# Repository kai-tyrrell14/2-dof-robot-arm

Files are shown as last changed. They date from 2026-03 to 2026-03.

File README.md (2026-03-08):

# 2 DOF Robotic Arm
An Arduino controlled 2-dof robotic arm capable of performing autonomous pick and place commands using calibrated servos and a gripper.
## 1. Demo
Robot Arm Demo

This demonstrates a simple pick and place routine using scripted joint movements.
## 2. Features
- 2-DOF robotic arm with gripper end effector
- Smooth joint motion control
- Soft-close gripper implemented
- Multi-command serial interface
- External power supply for reliable operation
- Automated pick and place routine

## 3. Hardware
| Component | Description |
|---|---|
| Arduino Uno | Microcontroller |
| PCA9685 Motor Driver | Servo controller |
| DS3225 Servo | Shoulder joint actuator |
| MG996R Servo | Elbow joint actuator |
| MG90S Servo | Gripper actuator |
| 6V 10A Power Supply | External servo power supply |

Servos are powered through external supply while Arduino and PCA9685 are powered through USB.

## 4. System Design
The system consists of three subsystems:
### 4.1 Mechanical System
A planar system consisting of two links with a shoulder joint and an elbow joint. The gripper is the end effector used to 
pick up and place objects.
### 4.2 Electrical System
An Arduino Uno sends commands to the PCA9685 which sends PWM signals to the servos
### 4.3 Control System
Commands are entered through the serial interface which interprets the commands and converts them into servo actuation.

System diagrams are available in the 'diagrams' folder.

## 5. User Interface
Commands are sent through the Arduino Serial Monitor using the following keys:
| Command | Description |
|---|---|
| 's <μs>' | Move shoulder servo to pulse width (μs) |
| 'e <μs>' | Move elbow servo to pulse width (μs) |
| 'o' | Open gripper |
| 'c' | Close gripper |
| 'h' | Move to home position |
| 'g' | Perform pick and place routine |
| 'p' | Print current joint state |
| 'r' | Release servo PWM |
| 'wait <μs>' | Pause sequence for (μs) |

## 6. Repository Structure
An overview of the files included in this repository:
- **'/CAD':** CAD models of mechanical components
- **'/analysis':** Calibration and engineering analysis
- **'/code':** Arduino control software
- **'/diagrams':** System design diagrams
- **'/docs':** Project documentation
- **'/electronics':** Wiring diagrams and pinout reference
- **'/media':** Demomstration images and videos

## 7. Engineering Challenges
A number of issues were encountered and solutions implemented:
- Shoulder joint servo was upgraded from MG996R to DS3225 after torque requirements were not being met
- A soft-close approach was implemented to prevent servo overloading after a servo was damaged.
- Motion smoothing and sequencing was implemented after stability issues were observed.

More information can be found in 'docs/engineering_challenges.md'

## 8. Future Improvements
Some potential improvements may include:
- Improving Base Stability
- Computer Vision Integration
- Automated Path Planning

More information can be found in 'docs/future_improvements.md'

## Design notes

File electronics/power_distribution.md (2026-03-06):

# Power Distribution
**Controller:** Arduino Uno

**Servo Driver:** PCA9685

**Servo Supply:** 6V DC (10A)

## 1. Overview
The system is powered through an external 6V power supply and the arduino logic is powered through USB.
All grounds are connected and provide a common reference for PWM signalling.

See 'wiring_diagram.png' for the wiring layout.

## 2. Power Sources
| Subsystem | Voltage | Source | Notes |
|---|---|---|---|
| Arduino Uno | 5V | USB | Logic |
| PCA9685 Logic | 5V | Arduino 5V -> VCC | I2C + PWM |
| Servos | 6V | External supply -> V+ | High current load |

## 3. Power Wiring
### 3.1 Servo Power
- External +6V -> PCA9685 V+
- PCA9685 V+ rail -> Servo V+

### 3.2 Ground / Reference
- External supply GND -> PCA9685 GND
- Arduino GND -> PCA9685 GND
- Servo GND -> PCA9685 GND

## 4. Risk Controls
### 4.1 Brownout Prevention
- Servo power separate from logic power
- External supply provides stable current during peak loads

### 4.2 Gripper Overheating Prevention
- Soft-close grip implemented
- PWM is released after gripper to avoid continous stall current

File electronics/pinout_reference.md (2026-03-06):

# Pinout Reference
**Controller:** Arduino Uno

**Servo Driver:** PCA9685

Refer to 'electronics/wiring_diagram.png'.

## 1. I2C Communication Interface
| Arduino Pin | PCA9685 | Function |
|---|---|---|
| A4 | SDA | I2C Data |
| A5 | SCL | I2C Clock |
| 5V | VCC | Logic Power |
| GND | GND | Common Ground |

## 2. Servo Channel Assignments
| PCA9685 Channel | Component | Purpose |
|---|---|---|
| CH0 | Shoulder Servo | Base joint rotation |
| CH1 | Elbow Servo | Elbow joint rotation |
| CH2 | Gripper Servo | Gripper operation |

## 3. Power Distribution
| Source | Destination | Description |
|---|---|---|
| 6V External Supply | PCA9685 | Servo Power Rail |
| External GND | Arduino GND | Common Ground |
| Arduino 5V | PCA9685 | Driver Logic Power |

## 4. Servo Wiring
| Wire Colour | Signal | Connected To |
|---|---|---|
| Red | V+ | PCA9685 V+ Rail |
| Black | GND | PCA9685 GND |
| Yellow | PWM | PCA9685 Channel Output |

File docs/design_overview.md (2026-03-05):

# Design Overview
## 1. System Details
This project consists of a small two degrees-of-freedom robotic arm capable of performing pick and place tasks. The arm
involves two rotational joints, the shoulder and elbow, and an end effector, the gripper. The system is controlled using an
Arduino Uno and a PCA9685 PWM motor driver which generates the servo control signals. The arm is capable of moving small objects, such as a dice, to from from predetermined positions using scripted joint movements.

## 2. Mechanical Design
The arm consists of two links which rotate about a stationary base. The links are driven at two joints through servo motors.
The gripper attached to the end of the second link is also driven by a servo motor.

The servo motors used are:
- Shoulder Joint: DS3225
- Elbow Joint: MG996R
- Gripper: MG90S

The shoulder joint is driven directly by the servo, while the elbow joint is driven through a pulley system.

## 3. Electrical Design
The system's electronics consist of:
- Arduino Uno microcontroller
- PCA9685 motor driver
- External 6V 10A power supply
- USB power supply

The Arduino Uno and PCA9685 are powered by the USB supply and control the systems logic. The PCA9685 provides PWM signals to the servos which are powered through the external 6V 10A power supply.

## 4. Control Design
The arm is controlled through commands entered into the serial interface which the code interprets and provides PWM commands through the arduino to the PCA9685 to the servos to perform the commanded tasks. The system allows for specific poses and positions to be saved and used to perform different routines, such as the pick and place routine.

## 5. Key Design Decisions
The following design decisions were implemeted to ensure the reliability and performance of the system:
- A PCA9685 motor driver was used to provide accurate and stable servo timing.
- Servo limits were calibrated to prevent mechanical binding and damage to servos.
- A soft-close approach was used to control the gripper and prevent overloading the servo.
- The logic power and servo actuation power were separated into their own circuits to prevent voltage drop and overloading of
  the arduino.

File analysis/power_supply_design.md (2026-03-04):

# Power Supply Design
This document outlines the power requirements for the entire robotic arm system. The system incorporates three different servo
types for the shoulder, elbow and gripper.

## 1. System Components
| Component | Supply | Notes |
|---|---|---|
| Arduino Uno | USB | Microcontroller |
| PCA9685 | Arduino 5V | PWM Driver |
| Shoulder Servo | 6V External | DS3225 Servo |
| Elbow Servo | 6V External | MG996R Servo |
| Gripper Servo | 6V External | MG90S Servo |

## 2. Estimated Servo Current
Current drawn by servos varies depending on load.
| Condition | DsS3225 (Shoulder) | MG996R (Elbow) | MG90S (Gripper) |
|---|---|---|---|
| Idle | ~20-50 mA | ~10-50 mA | ~10-20 mA |
| Moving (no load) | ~500 mA | ~500-900 mA | ~150-250 mA |
| Under Load | ~1.5 A | ~1.5-2 A | ~400-600 mA |
| Stall (worst case) | ~2.3 A | ~2.5 A | ~700 mA |

## 3. Worst Case Design Scenario
The worst case design scenario assumes all servos acting at stall conditions.
Worst case per servo:
- Shoulder (DS3225) = 2.3 A
- Elbow (MG996R) = 2.5 A
- Gripper (MG90S) = 0.7 A

Total peak demand:
2.3 A + 2.5 A + 0.7 A = 5.5 A

## 4. Logic Power Requirements
| Component | Current |
|---|---|
| Arduino Uno | ~50 mA |
| PCA9685 | ~10 mA |
Total pwer requirement ≈ 60 mA

## 5. Final Power Supply Design 
The final design for delivering power to the robotic arm involves separating servo actuation power and logic power into two
different circuits. This prevents voltage drop and ensures the Arduino Uno or PCA9685 do not draw excessive current. The power
must also safely meet the demands of the worst case design scenario.

The following power supplys are used in the system:
- Servo Actuation Power: External 6V 10A power supply
- Logic Power: USB powered

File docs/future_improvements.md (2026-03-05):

# Future Improvements
This document outlines potential improvements that could be implemented to increase the performance and functionality of the
robotic arm.
## Increased Base Stability
The stability of the base could be increased by increasing the weight of the base or rigidly attaching the base to a stable surface.
## Computer Vision Integration
Adding a camera and computer vision system would allow the system to detect objects and pick and place them, rather then 
rely on known positions.
## Automated Path Planning
Currently shoulder and elbow movement are performed sequentially, by adding path planning the arm would be able to move to certain locations in the most efficient manner with smoother motion.

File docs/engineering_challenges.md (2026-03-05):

# Engineering Challenges
This document summarises the main engineering challenges faced during the development of the robotic arm and the solutions that
were implemented.

## 1. Shoulder Torque Limitation
### 1.1 Issue
During the early testing of the shoulder joint, once link 2 was connected the joint struggled when rotated by a low torque servo.
### 1.2 Cause
Adding link 2 increases the torque requirements to rotate the shoulder joint.
### 1.3 Solution
The inital MG996R servo was upgraded to a higher torque DS3225 servo which provided the required torque and ensured stable
motion.

## 2. Gripper Servo Overloaded
### 2.1 Issue
During the initial testing of the gripper servo there was audible strain and eventually the servo failed and needed to be replaced.
### 2.2 Cause
The gripper servo was commanded to close past its limits and when gripping an object it attempts to close to this point which overloads the servo and causes permanent damage.
### 2.3 Solution
A soft-close approach was implemented in the code for gripper which prevents the gripper from loading past its limits and 
releases the servo to prevent overloading.

## 3. Arm Stability
### 3.1 Issue
The arm occasionally tipped forward when elbow was fully extended.
### 3.2 Cause
When fully extended the moment arm is increased which reduces the stability of the arm's base.
### 3.3 Solution
Motion sequencing and smoothing were implemented to increase stability.

## 4. Command Interface
### 4.1 Issue
Early versions of the code required single codes to be entered one at a time.
### 4.2 Cause
The command interface didn't support the entry of multiple commands.
### 4.3 Solution
A command splitter was implemented, allowing for the entry of a series of commands which could be performed sequentially.

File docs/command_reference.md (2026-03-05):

# Command Reference
This document outlines how to control the arm through the serial interface.
## 1. Command Format
Commands to the arm are entered through Arduino's Serial Monitor. Multiple commands can be performed in sequence by separating
them  with ':'.

For example:

s 1400; e 1200; h

## 2. Supported Commands
| Command | Description |
|---|---|
| 's <μs>' | Move shoulder servo to pulse width (μs) |
| 'e <μs>' | Move elbow servo to pulse width (μs) |
| 'o' | Open gripper |
| 'c' | Close gripper |
| 'h' | Move to home position |
| 'g' | Perform pick and place routine |
| 'p' | Print current joint state |
| 'r' | Release servo PWM |
| 'wait <μs>' | Pause sequence for (μs) |

## 3. Example Commands
s 1400; e 1300; o;

Moves shoulder and elbow to respective positions and opens gripper.

s 1700; e 1600; h; g
Moves shoulder and elbow to respective positions, returns home, performs pick and place routine.

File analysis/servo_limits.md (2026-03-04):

# Servo Limits Calibration
All limits were determined experimentally using incremental increases to determine where overloading occurs.

## 1. Summary Table
| Joint | Channel | Min (μs) | Max (μs) | Home (μs) | 
|---|---|---|---|---|
| Shoulder | CH0 | 700 | 2300 | 1200 |
| Elbow | CH1 | 700 | 1700 | 800 |
| Gripper | CH2 | 500 (open) | 950 (soft-close) | 950 |

## 2. Calibration Method
1. Servo was moved in small increments (5-10 μs).
2. Movement was stopped as soon as binding occured.
3. Limits were set 50 μs from these points to ensure safe limits.
4. These limits were then validated through repeated motion.
5. These final values were set as constraints in the code.

## 3. Design Intent

These servo limits are clearly defined and documented in order to:
- Prevent mechanical binding
- Prevent servo overloading
- Prevent gear stripping
- Ensure system reliability

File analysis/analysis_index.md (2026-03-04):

# Analysis Index
The files in this folder outline the calibration and analysis methods used in the design of the robotic arm.

## 1. Key Outcomes
- Calibrated safe servo operating limits and ensured constraints in code.
- After overloading a servo resulting in damage, a soft-close was implemented for the gripper.
- Resolved potential tipping risks by ensuring proper order of servo actuation.

## 2. Documents
- 'servo_limits.md' : Outlines final servo pulse ranges and home position.
- 'calibration_results.md' : Summarises calibration testing, constraints and validation.
- 'power_supply_design.md' : Estimated current demand for servo power distribution.
- 'stability_notes.md' : Observed behaviour of robot arm stability and when tipping may occur.

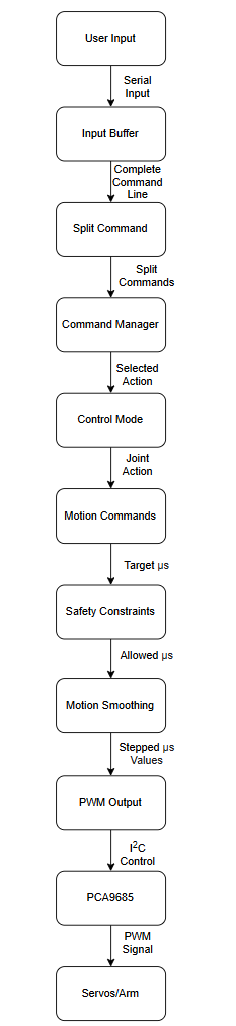
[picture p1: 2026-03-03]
diagrams/control_architecture.png

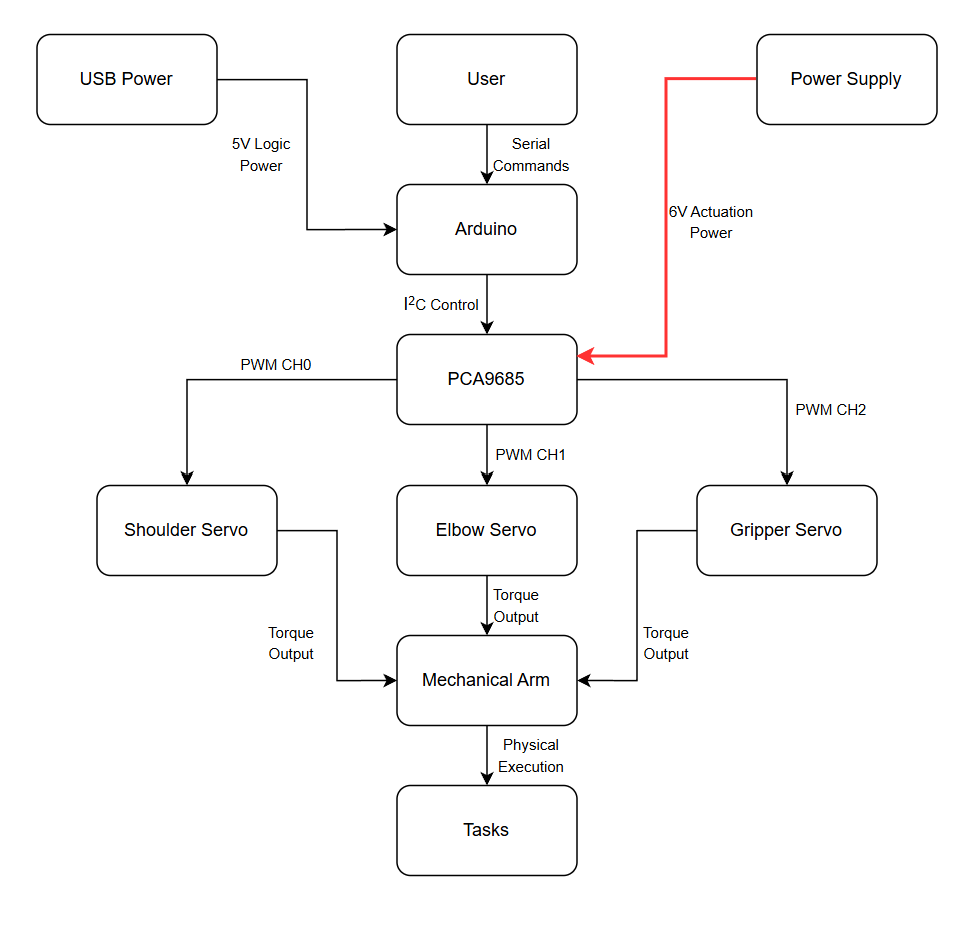
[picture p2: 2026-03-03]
diagrams/system_block_diagram.png

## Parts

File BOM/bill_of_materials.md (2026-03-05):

# Bill of Materials
| Item | Component | QTY |
|---|---|-----|
| 1 | 3D Printed Parts | 1 set |
| 2 | Arduino Uno | 1 | 
| 3 | PCA9685 Motor Driver | 1 |
| 4 | DS3225 Servo | 1 |
| 5 | MG996R Servo | 1 |
| 6 | MG90S Servo | 1 |
| 7 | 8mm Shaft | 1 |
| 8 | 5mm Shaft | 1 |
| 9 | 608 Bearing | 2 |
| 10 | 625 Bearing | 2 |
| 11 | 25T Metal Round Servo Horn | 1 |
| 12 | Servo Spline Shaft | 1 |
| 13 | GT2 Timing Belt | 1 |
| 14 | 20T GT2 Pulley | 1 |
| 15 | 40T GT2 Pulley | 1 |
| 16 | 5mm Shaft Collar | 2 |
| 17 | 8mm Shaft Coupling | 1 |
| 18 | 5mm Shaft Coupling | 1 |
| 19 | Gripper | 1 |
| 20 | M3 Screws & Nuts | Various |
| 21 | 6V 10A Power Supply | 1 |

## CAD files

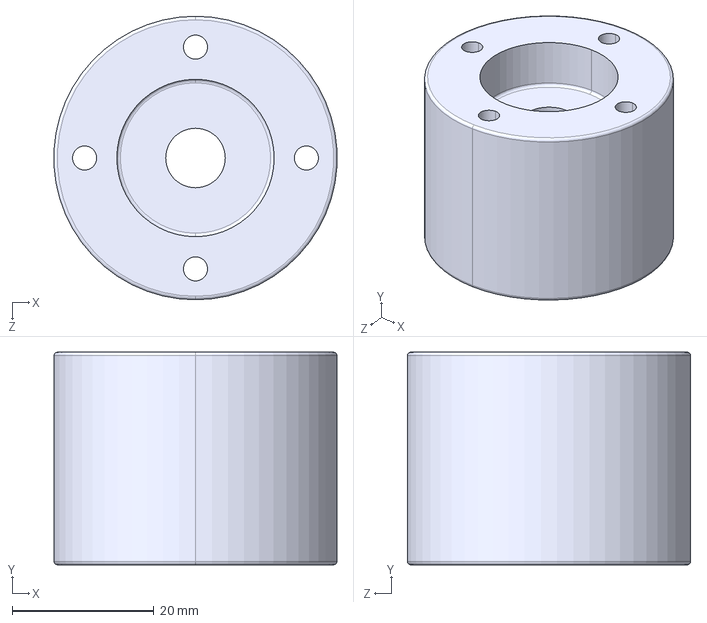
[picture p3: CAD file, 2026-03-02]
CAD/exports/bearing_tower.STEP
39.9 x 30.0 x 40.0 mm

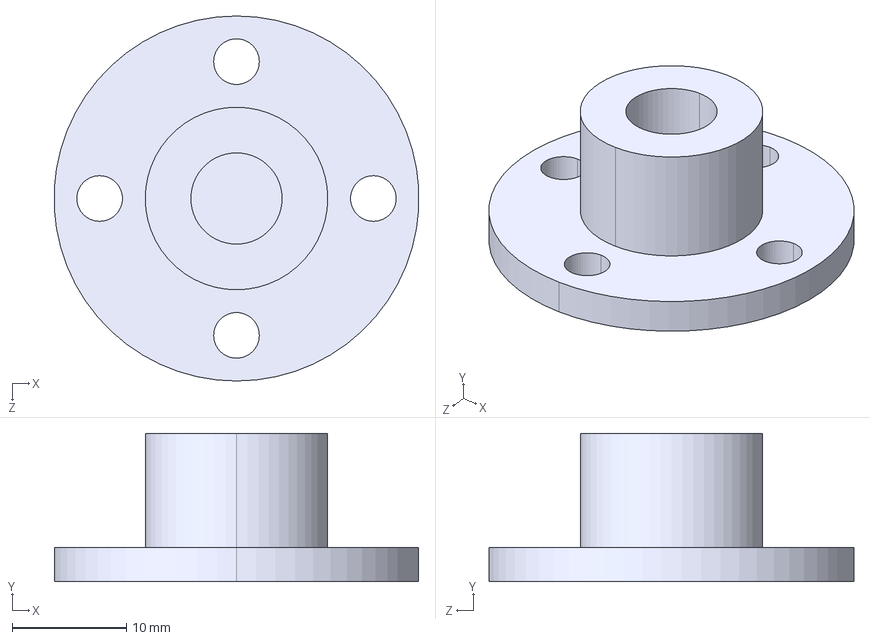
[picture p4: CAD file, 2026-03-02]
CAD/exports/shaft_hub_base.STEP
32.0 x 13.0 x 32.0 mm

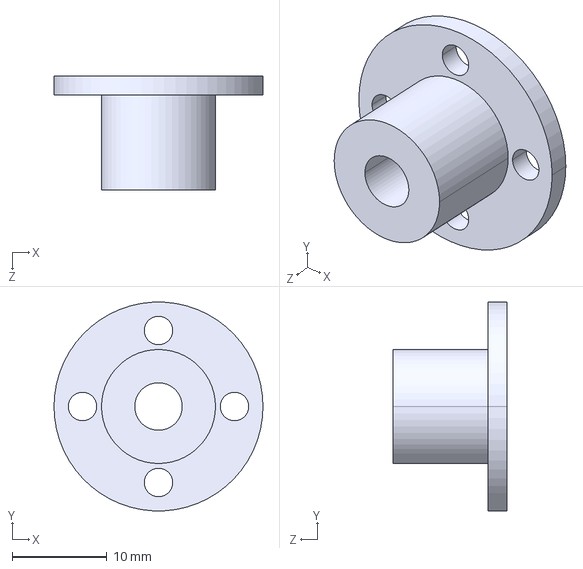
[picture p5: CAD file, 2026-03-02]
CAD/exports/link_2_shaft_hub.STEP
22.0 x 22.0 x 12.0 mm

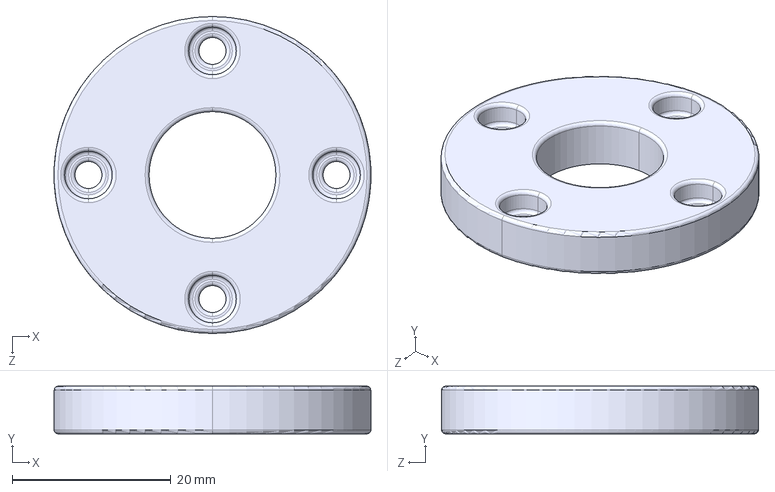
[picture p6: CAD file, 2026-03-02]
CAD/exports/top_retainer_plate.STEP
40.0 x 6.00 x 40.0 mm

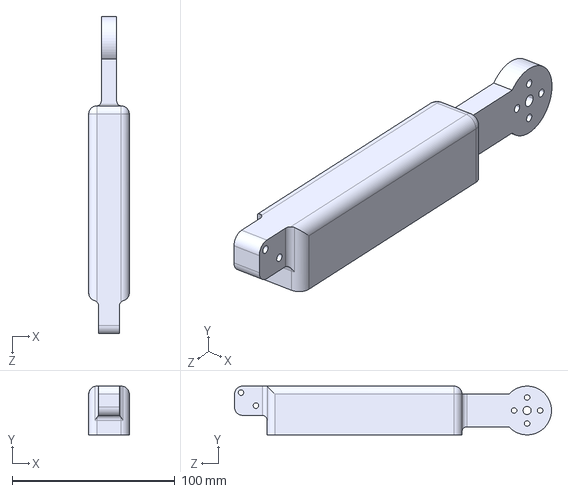
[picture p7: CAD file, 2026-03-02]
CAD/exports/link_2.STEP
25.0 x 30.0 x 195.0 mm

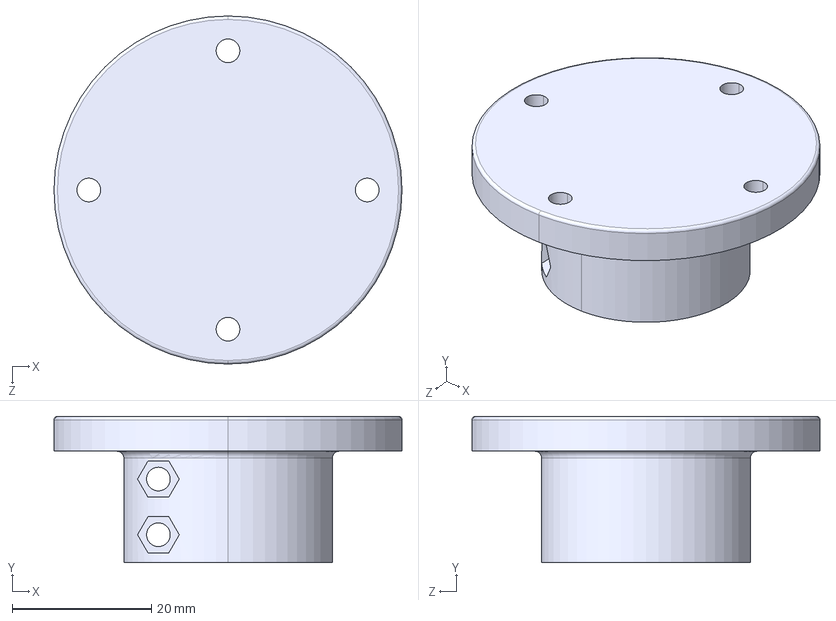
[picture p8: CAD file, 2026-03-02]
CAD/exports/link_1_shaft_hub.STEP
50.0 x 21.0 x 50.0 mm

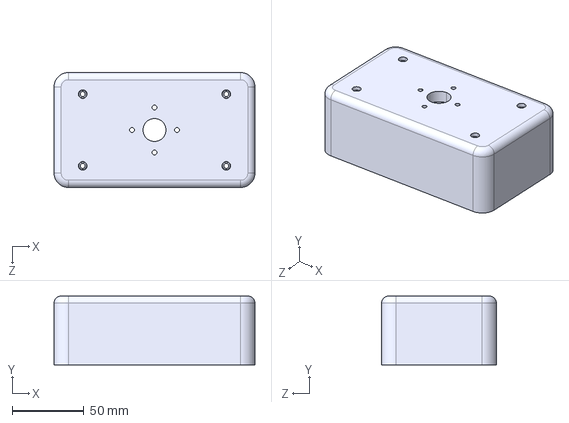
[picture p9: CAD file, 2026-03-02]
CAD/exports/base_plate_top.STEP
140.0 x 48.0 x 80.0 mm

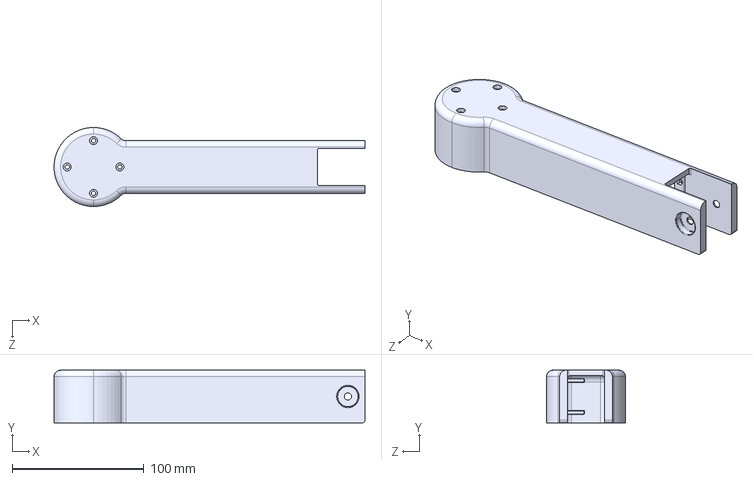
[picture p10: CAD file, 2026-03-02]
CAD/exports/link_1.STEP
236.0 x 40.0 x 60.0 mm

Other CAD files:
CAD/exports/base_plate_bottom.STEP
CAD/parts/base_plate_bottom.SLDPRT
CAD/parts/base_plate_top.SLDPRT
CAD/parts/bearing_tower.SLDPRT
CAD/parts/link_1.SLDPRT
CAD/parts/link_1_shaft_hub.SLDPRT
CAD/parts/link_2.SLDPRT
CAD/parts/link_2_shaft_hub.SLDPRT
CAD/parts/shaft_hub_base.SLDPRT
CAD/parts/top_retainer_plate.SLDPRT

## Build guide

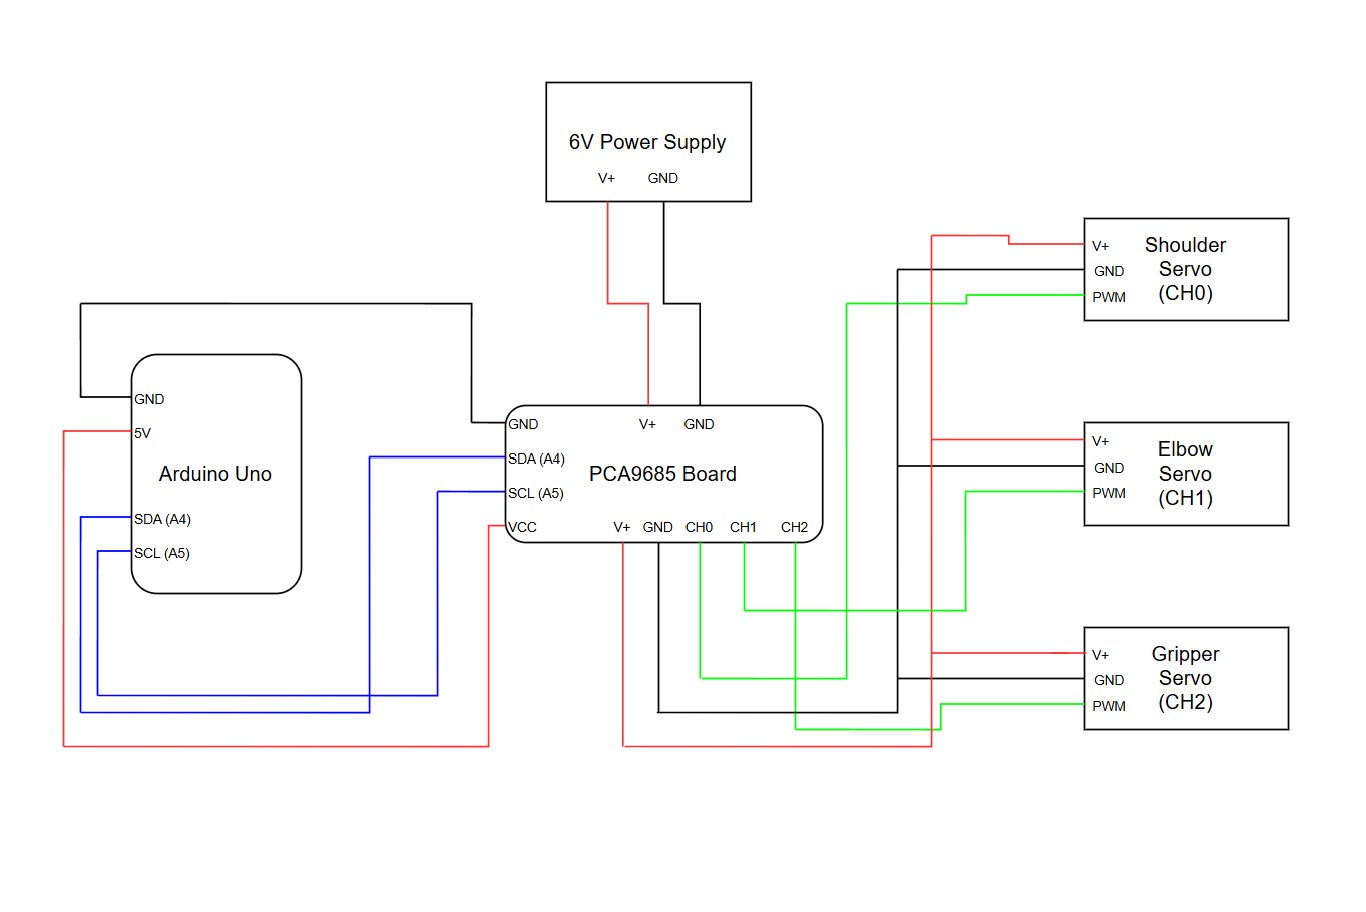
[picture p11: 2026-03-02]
electronics/wiring_diagram.png

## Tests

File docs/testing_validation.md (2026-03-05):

# Testing Validation
This document outlines he methods to verify the system works as expected.
## 1. Testing Objectives
The objectives that were tested and verified:
- Each joint could move through its calibrated servo limits
- Joint movements were performed smoothly
- Small objects could be gripped and released
- The pick and place routine was performed correctly
- The system can operate without any damage to or overheating of servos

## 2. Testing Procedures
The system was tested through the serial interface.

Manual commands were entered to test each servo through their calibrated ranges and multiple open and close gripper commands
were performed.

Repeated automated pick and place routines were then executed to ensure motion and positioning were accurate and repeatable.

## 3. Testing Results
| Test | Descritption | Results |
|---|---|---|
| Joint Movement | Shoulder and elbow moved through calibrated servo limits| Pass |
| Smooth Motion | Servos moved smoothly without sudden jumps | Pass |
| Gripper Operation | Object successfully gripped and released | Pass |
| Pick and Place Routine | The pick and place routine performed multiple times in succession | Pass |

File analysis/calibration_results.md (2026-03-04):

# Calibration Results
This document summarises the methods for calibrating the servos used for the robotic arm. 
This calibration was necessary before automated routines, such as pick and place, can be performed.

## 1. Test Method
- Controller: Arduino Uno + PCA9685
- Method: incremental pulse stepping
- Observation criteria: mechanical binding, audible strain, overheating
- Validation: repeated motion cycles without any issues

Final operating limits shown in 'servo_limits.md'
## 2. Calibration of Servos
### 2.1 Shoulder (CH0)
**Experimental range:** 600-2400 μs

**Key observations:**
- Binding observed below 640 μs
- Binding observed above 2350 μs
- Shoulder movement at high speeds with elbow fully extended may result in tipping

**Validation:**
- Repeated motion cycles within servo limits resulted in no binding

### 2.2 Elbow (CH1)
**Experimental range:** 600-1800 μs

**Key observations:**
- Increasing the pulse width moves elbow downwards
- Binding observed below 650 μs
- Binding observed above 1770 μs

**Validation:**
- Repeated motion cycles within servo limits resulted in no binding

### 2.3 Gripper (CH2)
**Initial issue:**
- Original command for closing gripper resulted in sustained overloading of the SG90 servo
- As a result one servo failed from being overloaded for too long
- Gripper was driven to stall torque near limit

**Resolution:**
- A soft-close was implemented which closes the gripper enough to grip an object, before releasing the servo to prevent extended overloading

**Validation:**
- Repeated grip and release cycles with soft-close without failure

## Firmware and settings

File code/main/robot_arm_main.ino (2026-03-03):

#include <Wire.h>
#include <Adafruit_PWMServoDriver.h>

Adafruit_PWMServoDriver pwm(0x40);

// Channels
// Channels mapped as per 'pinout_reference.md' so to change channels only these values 
// must be changed.
#define SHOULDER_CH 0
#define ELBOW_CH    1
#define GRIPPER_CH  2

// Limits
// Limits have been determined experimentally, where going past these limits can overload
// servos.
const int SHOULDER_MIN_US = 700;
const int SHOULDER_MAX_US = 2300;

const int ELBOW_MIN_US = 700;
const int ELBOW_MAX_US = 1700;

const int GRIP_OPEN_US       = 500;
const int GRIP_CLOSE_SOFT_US = 950;

// Home Position
// This position is used as a reference for testing and demonstrations.
const int SHOULDER_HOME_US = 1200;
const int ELBOW_HOME_US    = 800;

// The auto settings allow for faster movements to known positions, such as home or pick
// and place. The manual settings are slower for manual inputs.
const int AUTO_STEP_US   = 10;  
const int AUTO_DELAY_MS  = 10;

const int MANUAL_STEP_US  = 5;  
const int MANUAL_DELAY_MS = 4;

// Initial Position
int sh_us = SHOULDER_HOME_US;
int el_us = ELBOW_HOME_US;
int gr_us = GRIP_CLOSE_SOFT_US;

// Poses
struct Pose { int shoulder; int elbow; };

Pose HOME       = { 1200,  800 };
Pose ABOVE_PICK = { 1200, 1200 };  
Pose PICK_DOWN  = { 1200, 1700 };  

Pose ABOVE_PLACE= { 1500, 1200 };  
Pose PLACE_DOWN = { 1500, 1700 };

Pose LIFT_PICK  = { 1200, 1050 };  
Pose LIFT_PLACE = { 1500, 1050 };  


// Converts microseconds to ticks to allow for consistent pulse widths through each channel.
int usToTicks(int us) {
  us = constrain(us, 400, 2500);
  return (int)((us * 4096L) / 20000L);  
}

// Uses the value above to set the PWM for the servos, where the limits and positions
// above can be changed with changing logic below.
void setServoUs(int ch, int us) {
  pwm.setPWM(ch, 0, usToTicks(us));
}

// Releases servo to prevent overloading.
void releaseServo(int ch) {
  pwm.setPWM(ch, 0, 0);
}

// Using the stepped motion below, sudden acceleration and peak torque are reduced.
void moveTo(int ch, int &current, int target, int stepUs, int delayMs) {
  target = constrain(target, 400, 2500);

  if (target > current) {
    for (int u = current; u <= target; u += stepUs) {
      setServoUs(ch, u);
      delay(delayMs);
    }
  } else {
    for (int u = current; u >= target; u -= stepUs) {
      setServoUs(ch, u);
      delay(delayMs);
    }
  }
  current = target;
}

void printState() {
  Serial.print("Shoulder_us="); Serial.print(sh_us);
  Serial.print("  Elbow_us=");  Serial.print(el_us);
  Serial.print("  Gripper_us=");Serial.println(gr_us);
}

// The code below sets the order of movement. The elbow is moved before the shoulder to 
// reduce the risk of the arm tipping.
void moveArm(Pose p, bool elbowFirst=true) {
  p.shoulder = constrain(p.shoulder, SHOULDER_MIN_US, SHOULDER_MAX_US);
  p.elbow    = constrain(p.elbow,    ELBOW_MIN_US,    ELBOW_MAX_US);

  if (elbowFirst) {
    moveTo(ELBOW_CH,    el_us, p.elbow,    AUTO_STEP_US, AUTO_DELAY_MS);
    moveTo(SHOULDER_CH, sh_us, p.shoulder, AUTO_STEP_US, AUTO_DELAY_MS);
  } else {
    moveTo(SHOULDER_CH, sh_us, p.shoulder, AUTO_STEP_US, AUTO_DELAY_MS);
    moveTo(ELBOW_CH,    el_us, p.elbow,    AUTO_STEP_US, AUTO_DELAY_MS);
  }
}

void gripperOpen() {
  moveTo(GRIPPER_CH, gr_us, GRIP_OPEN_US, AUTO_STEP_US, AUTO_DELAY_MS);
  releaseServo(GRIPPER_CH);
}

// This function ensures that the gripper is able to pick up an object with overloading and
// damaging the servo.
void gripperCloseSoft(int holdMs = 150) {
  int approach = (GRIP_OPEN_US + GRIP_CLOSE_SOFT_US) / 2;
  moveTo(GRIPPER_CH, gr_us, approach, AUTO_STEP_US, AUTO_DELAY_MS);
  delay(60);

  moveTo(GRIPPER_CH, gr_us, GRIP_CLOSE_SOFT_US, AUTO_STEP_US, AUTO_DELAY_MS);
  // This delay ensures that the gripper properly grips the object.
  delay(holdMs);
  // This release prevents holding for too long and overloading.
  releaseServo(GRIPPER_CH);
}

// Pick and Place Routine
// Repeatable sequence for testing and demonstration.
void runPickPlace() {
  moveArm(ABOVE_PICK, true);  delay(150);
  gripperOpen();              delay(120);

  moveArm(PICK_DOWN, false);  delay(180);
  gripperCloseSoft(180);      delay(120);

  moveArm(LIFT_PICK, true);   delay(150);

  moveArm(ABOVE_PLACE, true); delay(150);

  moveArm(PLACE_DOWN, false); delay(180);
  gripperOpen();              delay(150);

  moveArm(LIFT_PLACE, true);  delay(150);

  moveArm(HOME, true);        delay(150);
  gripperCloseSoft(150);

  releaseServo(SHOULDER_CH);
  releaseServo(ELBOW_CH);
}

// Manual Servo Operation
void gotoShoulderUs(int targetUs) {
  targetUs = constrain(targetUs, SHOULDER_MIN_US, SHOULDER_MAX_US);
  moveTo(SHOULDER_CH, sh_us, targetUs, MANUAL_STEP_US, MANUAL_DELAY_MS);
}

void gotoElbowUs(int targetUs) {
  targetUs = constrain(targetUs, ELBOW_MIN_US, ELBOW_MAX_US);
  moveTo(ELBOW_CH, el_us, targetUs, MANUAL_STEP_US, MANUAL_DELAY_MS);
}


// The code below allows for the commanding of positions to move the robotic arm.
String line;

String trimCopy(String s) { s.trim(); return s; }

bool parseNumberAfter(const String &s, int &out) {
  String t = s;
  t.trim();
  if (t.length() == 0) return false;
  long v = t.toInt();
  if (v == 0 && t != "0") return false;
  out = (int)v;
  return true;
}

void execOne(String cmd) {
  cmd.trim();
  if (cmd.length() == 0) return;

  cmd.replace("=", " ");
  cmd.trim();

  int sp = cmd.indexOf(' ');
  String head = (sp >= 0) ? cmd.substring(0, sp) : cmd;
  String rest = (sp >= 0) ? cmd.substring(sp + 1) : "";
  head.trim(); rest.trim();

  if (head.equalsIgnoreCase("help") || head.equals("?")) {
    Serial.println("Use: s <us>; e <us>; o; c; g; h; p; r; wait <ms>");
    return;
  }
  if (head.equalsIgnoreCase("p")) { printState(); return; }
  if (head.equalsIgnoreCase("o")) { gripperOpen(); return; }
  if (head.equalsIgnoreCase("c")) { gripperCloseSoft(150); return; }
  if (head.equalsIgnoreCase("g")) { runPickPlace(); return; }
  if (head.equalsIgnoreCase("h")) {
    moveArm(HOME, true);
    gripperCloseSoft(150);
    releaseServo(SHOULDER_CH);
    releaseServo(ELBOW_CH);
    return;
  }
  if (head.equalsIgnoreCase("r")) {
    releaseServo(SHOULDER_CH);
    releaseServo(ELBOW_CH);
    return;
  }

  if (head.equalsIgnoreCase("wait") || head.equalsIgnoreCase("w")) {
    int ms;
    if (!parseNumberAfter(rest, ms)) { Serial.println("wait needs ms, e.g. wait 500"); return; }
    ms = constrain(ms, 0, 20000);
    delay(ms);
    return;
  }

  if (head.equalsIgnoreCase("s")) {
    int target;
    if (!parseNumberAfter(rest, target)) { Serial.println("s needs a number, e.g. s 1200"); return; }
    gotoShoulderUs(target);
    return;
  }
  if (head.equalsIgnoreCase("e")) {
    int target;
    if (!parseNumberAfter(rest, target)) { Serial.println("e needs a number, e.g. e 1200"); return; }
    gotoElbowUs(target);
    return;
  }

  Serial.print("Unknown cmd: "); Serial.println(cmd);
}

// This code allows for multiple commands to be entered at once, which will be commanded 
// in order.
void execSequence(String seq) {
  seq.replace(",", ";");

  int start = 0;
  while (start < (int)seq.length()) {
    int end = seq.indexOf(';', start);
    if (end < 0) end = seq.length();

    String cmd = seq.substring(start, end);
    cmd.trim();
    if (cmd.length() > 0) {
      execOne(cmd);
    }
    start = end + 1;
  }
}

// Command Instructions
void printHelp() {
  Serial.println("=== Multi-command control ===");
  Serial.println("Separate commands with ';' (or ','). Examples:");
  Serial.println("  s 1400; e 1200; o");
  Serial.println("  s=1200; e=1700; c; wait 500; s 1500; e 1200; o");
  Serial.println("Commands: s <us>, e <us>, o, c, g, h, p, r, wait <ms>");
  Serial.println("Note: set Serial Monitor line ending = Newline (or Both NL&CR).");
  Serial.println("=============================");
}

void setup() {
  Serial.begin(9600);
  pwm.begin();
  pwm.setPWMFreq(50);
  delay(10);

  Serial.println("Robot Arm Ready (multi-command + pick/place).");
  printHelp();

  // This starts the arm in the home position for ease of testing and demonstration.
  moveArm(HOME, true);
  delay(150);
  gripperCloseSoft(150);
  printState();
}

void loop() {
  while (Serial.available()) {
    char c = (char)Serial.read();
    if (c == '\n') {
      String cmdLine = line;
      line = "";
      cmdLine.trim();
      if (cmdLine.length() > 0) {
        execSequence(cmdLine);
      }
    } else if (c != '\r') {
      line += c;
      if (line.length() > 140) line = line.substring(0, 140);
    }
  }
}

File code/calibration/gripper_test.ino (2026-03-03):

#include <Wire.h>
#include <Adafruit_PWMServoDriver.h>

Adafruit_PWMServoDriver pwm(0x40);

// Channel mapped as per 'pinout_reference.md' so to change channel only this value 
// must be changed.
#define GRIPPER_CH 2

// Limits to determine the upper and lower bounds
const int SERVO_US_MIN = 400;
const int SERVO_US_MAX = 2500;

// Using these steps reduces sudden torque spikes.
int stepUs = 5;
int stepDelayMs = 6;

int gr_us = 700;

// Converts microseconds to ticks to allow for consistent pulse width.
int usToTicks(int us) {
  us = constrain(us, SERVO_US_MIN, SERVO_US_MAX);
  return (int)((us * 4096L) / 20000L); // 50Hz => 20,000 us
}

// Uses the value above to set the PWM for the servo, where the limits and positions
// above can be changed without changing logic below.
void setServoUs(int ch, int us) {
  pwm.setPWM(ch, 0, usToTicks(us));
}

// Releases servo to prevent overloading.
void releaseServo(int ch) {
  pwm.setPWM(ch, 0, 0);
}

// Using the stepped motion below, sudden acceleration and peak torque are reduced.
void moveToUs(int ch, int &current, int target) {
  target = constrain(target, SERVO_US_MIN, SERVO_US_MAX);

  int dir = (target >= current) ? 1 : -1;
  for (int u = current; u != target; u += dir * stepUs) {
    setServoUs(ch, u);
    delay(stepDelayMs);

    // prevent overshoot with step size
    if ((dir > 0 && u + stepUs > target) || (dir < 0 && u - stepUs < target)) break;
  }
  setServoUs(ch, target);
  current = target;
}

// Command Instructions
void printHelp() {
  Serial.println("\n=== Gripper Test (PCA9685 CH2) ===");
  Serial.println("Commands:");
  Serial.println("  o <us>      : go to OPEN value (example: o 500)");
  Serial.println("  c <us>      : go to CLOSE value (example: c 950)");
  Serial.println("  g <us>      : go to any pulse (example: g 750)");
  Serial.println("  step <us>   : set step size (example: step 5)");
  Serial.println("  delay <ms>  : set step delay (example: delay 6)");
  Serial.println("  r           : release PWM (stop holding torque)");
  Serial.println("  p           : print current value");
  Serial.println("  help        : show this help");
  Serial.println("Tip: Set Serial Monitor line ending = Newline");
  Serial.println("=================================\n");
}

String line;

bool parseIntArg(String s, int &out) {
  s.trim();
  if (s.length() == 0) return false;
  long v = s.toInt();
  if (v == 0 && s != "0") return false;
  out = (int)v;
  return true;
}

// The code below takes the input from the user and splits into commands to send to the servo.
void handleLine(String cmd) {
  cmd.trim();
  if (cmd.length() == 0) return;

  int sp = cmd.indexOf(' ');
  String head = (sp >= 0) ? cmd.substring(0, sp) : cmd;
  String rest = (sp >= 0) ? cmd.substring(sp + 1) : "";
  head.trim(); rest.trim();

  if (head.equalsIgnoreCase("help") || head.equals("?")) { printHelp(); return; }
  if (head.equalsIgnoreCase("p")) {
    Serial.print("gr_us="); Serial.print(gr_us);
    Serial.print("  stepUs="); Serial.print(stepUs);
    Serial.print("  stepDelayMs="); Serial.println(stepDelayMs);
    return;
  }
  if (head.equalsIgnoreCase("r")) { releaseServo(GRIPPER_CH); Serial.println("Released gripper PWM"); return; }

  if (head.equalsIgnoreCase("step")) {
    int v; if (!parseIntArg(rest, v)) { Serial.println("step needs number"); return; }
    stepUs = constrain(v, 1, 50);
    Serial.print("stepUs="); Serial.println(stepUs);
    return;
  }
  if (head.equalsIgnoreCase("delay")) {
    int v; if (!parseIntArg(rest, v)) { Serial.println("delay needs number"); return; }
    stepDelayMs = constrain(v, 0, 50);
    Serial.print("stepDelayMs="); Serial.println(stepDelayMs);
    return;
  }

  if (head.equalsIgnoreCase("o") || head.equalsIgnoreCase("c") || head.equalsIgnoreCase("g")) {
    int target;
    if (!parseIntArg(rest, target)) { Serial.println("Command needs <us>"); return; }
    target = constrain(target, SERVO_US_MIN, SERVO_US_MAX);

    Serial.print("Moving gripper -> "); Serial.println(target);
    moveToUs(GRIPPER_CH, gr_us, target);

    Serial.print("Now at "); Serial.println(gr_us);
    return;
  }

  Serial.print("Unknown command: "); Serial.println(cmd);
}

void setup() {
  Serial.begin(9600);
  pwm.begin();
  pwm.setPWMFreq(50);
  delay(10);

  Serial.println("Gripper test ready.");
  printHelp();

  moveToUs(GRIPPER_CH, gr_us, gr_us);
  releaseServo(GRIPPER_CH);
}

void loop() {
  while (Serial.available()) {
    char c = (char)Serial.read();
    if (c == '\n') {
      String cmd = line; line = "";
      handleLine(cmd);
    } else if (c != '\r') {
      line += c;
      if (line.length() > 80) line = line.substring(0, 80);
    }
  }
}

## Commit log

2026-03-03 Add pinout reference for 2-DOF robotic arm
2026-03-03 Add power distribution documentation for robotic arm
    Documented power distribution details for a 2-DOF robotic arm, including power sources, wiring, and risk controls.
2026-03-03 Add servo limits calibration documentation
    Documented servo limits calibration process and results.
2026-03-03 Add calibration results documentation
    Document methods and results for servo calibration in robotic arm.
2026-03-04 Revise power supply design details for robotic arm
    Updated the power supply section to detail the final design for the robotic arm, including separation of servo and logic power circuits.
2026-03-04 Replace power_budget.md with power_supply_design.md
2026-03-04 Revise calibration results document structure
    Renumbered sections and updated headings for clarity.
2026-03-04 Update section header for calibration of servos
2026-03-04 Update sections and formatting in power supply design
2026-03-04 Fix formatting in power supply design document
2026-03-04 Update servo limits calibration documentation sections
2026-03-05 Add design overview for robotic arm project
    Added detailed sections on system, mechanical, electrical, control design, and key design decisions for the robotic arm project.
2026-03-05 Add command reference for arm control
    Added command reference documentation for controlling the arm via serial interface, including command format, supported commands, and examples.
2026-03-05 Summarize engineering challenges and solutions
    Document engineering challenges and their solutions during robotic arm development.
2026-03-05 Document potential improvements for robotic arm
    Added a section outlining potential improvements for the robotic arm, including stability, computer vision integration, and automated path planning.
2026-03-05 Create bill_of_materials.md with item list
    Added a Bill of Materials table with components and quantities.
2026-03-05 Revise Bill of Materials with new components
    Updated the Bill of Materials to include additional components and improved formatting.
2026-03-06 Update title of power distribution document
    Removed specific reference to '2-DOF Robotic Arm' in the title.
2026-03-06 Add reference to wiring diagram in pinout reference
    Added a reference to the wiring diagram for clarity.
2026-03-06 Change header level for Ground / Reference section
